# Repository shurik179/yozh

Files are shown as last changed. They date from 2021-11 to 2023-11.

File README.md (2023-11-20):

# Yozh Robot
Yozh is a small tracked  robot programmable in CircuitPython. 
It was  inspired by  Pololu's Zumo, but has numerous improvements over it. 
It was created by shurik179 for a robotics class at SigmaCamp.

The project description and logs are posted on Hackaday: 
https://hackaday.io/project/193665-yozh-robot. 
Detailed  user documentation is available at http://yozh.rtfd.io. 

## Status
Version 4 is mostly finished, working on documentation and fine-tuning 
various PID controllers. 

## Structure of this repository
* `docs`: documentation (used to produce docs at http://yozh.rtfd.io)
* `hardware`: design files for the custom electronics boards, BOM, etc.
* `board_support_package`: bootloader and packeg to have the secondary MCU 
   supported in Arduino IDE. Only needed fro uploading the firmware - end 
   users do not need this. 
* `firmware`: firmware for secondary MCU
* `circuitpython_library`: Circuit Python user library

## License
Ecept as noted below, all components (hardware, software, documentation) are
copyright by Alexander Kirillov  and are  released under MIT license.
See file LICENSE in this directory for full text of the license.

Circuit Python librabries included in circuitpython_library/lib are copyright by Adafruit, see
https://github.com/adafruit/Adafruit_CircuitPython_Bundle . They are released under MIT License.

Fonts included with Circuit Python library are released under SIL Open Font License.
See LICENSE file in directory circuitpython_library/fonts

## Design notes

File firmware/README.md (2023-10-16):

# Yozh  Firmware

This folder  contains the firmware and
necessary support files for Yozh robot.

Since Yozh comes with the firmware pre-installed, most users do not need
any of the files in this directory. You only need to use it if you want to
understand the inner workings of the firmware, or to create your own modified
version of the firmware. Note: the authors of the firmware provide no technical
support for modifying the firmware; do it at your own risk.

## Building the firmware from source
This information is for advanced users only. Use at your own risk!!

It is assumed that you have some experience with Arduino, so the instructions
are brief. This is intentional, to discourage inexperienced users.

To build the firmware from the source, you need the following software installed
on your computer:

1.  Arduino IDE (version 1.8 or later).

2. Board definition files -- see instructions below

3. Required libraries:

   *  FlashStorage

   All of these libraries can be installed using library manager built into Arduino IDE

4. After completing the steps above,  restart the Arduino IDE and select
`Adafruti Crickit M0` in *Tools->Board* menu.

You are now ready to build and upload new firmware from source. Download the
contents of this  repository as a zip file, unpack, and find inside it folder
`firmware/yozh-firmware`. Move it  to Arduino sketchbook folder. Now find in that
folder file  `yozh-firmware.ino` and open it in Arduino IDE. Edit is as you
like and upload to the board in the usual way.

### Board definition files
For step 2 above, you need to install the board definition files for Yozh main
board.  The easiest way to do it is to reuse the board definitions
provided by Adafruit for their Crickit board, just changing some files, as
follows:

1. Install Adafruit's board support package for SAMD-based boards, as described
[here](https://learn.adafruit.com/adafruit-feather-m0-basic-proto/setup). Please
use version 1.5.13, **even if later versions are available** (most likely, using
later versions would also be OK, but it was not tested.)

2. Find the installed package files.  To do this, first find the folder with
Arduino configuration data;  depending on your OS and version of Arduino IDE, it
can be either `<username>\AppData\Local\Arduino15` (Windows),
`<username>\Documents\ArduinoData\` (Windows 10, using Arduino IDE installed
from Windows store), or `/home/<user>/.arduino15/` (Linux).

    Once you found the Arduino configuration data folder, navigate to `\packages\adafruit\hardware\samd\1.5.13\variants\crickit_m0`.

3. Download two files `variant.cpp` and `variant.h` from `boardDefinitions`
folder in this repository and use them to replace the corresponding files in
`crickit_m0` folder.

4. Restart Arduino IDE.

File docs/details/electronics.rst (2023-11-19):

Electronics
===========
The robot is controlled by two microcontrollers (MCU):

* Main (master) MCU: `ESP32-S3 Reverse TFT Feather  <https://www.adafruit.com/product/5691>`__.
  This MCU is programmed by the user in CircuitPython. Provided CircuitPython
  library, documented in :ref:`Yozh Library Guide <library>`, provides convenient
  functions for using all features of the robot.

* Secondary (slave) MCU: SAMD21G18A. This MCU is responsible for all low-level
  operations, converting high-level commands coming from main MCU into signals
  sent to motors, servos and more, thus freeing pins and other
  resources of the main MCU for other purposes.  Secondary MCU  is also responsible for counting
  the encoder pulses and running the PID control loop maintaining motor speed.
  This MCU comes preloaded with firmware, written in C++ (using Arduino IDE).
  Normally, the user shouldn't need to touch this firmware.

The two MCUs talk to each other  using I2C communication protocol; main MCU acts as
the master on the I2C bus, and the secondary acts as slave.

Some of Yozh hardware is directly controlled by the main MCU, without going
through the secondary one:

* TFT  display

* Buttons

* Buzzer

* Distance sensors

* Two indicator NeoPixel leds

* battery voltage monitor

Everything else -- motors, encoders, servos, reflectance sensor
array,  Inertial Motion Unit -- is handled by the
secondary MCU.

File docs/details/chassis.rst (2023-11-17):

Chassis and motors
===================
Yozh robot uses custom-made chassis, using 
`silicone tracks <https://www.pololu.com/product/3034>`__ by Pololu together with two
`75:1 High Power 6V microgear motors <https://www.pololu.com/product/2215>`__. The
motors are equipped with encoders (rotation counters), for speed control. The
motors are controlled by DRV8833 motor driver by TI.

Maximal speed of the robot is FIXME m/s.

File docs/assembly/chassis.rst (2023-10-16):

Assembling the chassis
======================
Take the Zumo chassis kit and open it. Make sure you have all components
as listed in `Zumo chassis user guide <https://www.pololu.com/docs/0J54/1>`__.
Discard the acrylic plate - we wont' be using it.

Now follow these steps:

1. Turn the chassis upside down. Remove the cover  from the battery
   compartment of the chassis and insert the double battery contacts in the
   slots as shown in the photo below, paying attention to orientation.
   Leave two single contacts for later.

2. Insert 4 M2.5 screws from Yozh kit in the
   holes as shown in the photo below. It should be a tight fit -- use a screwdriver
   to drive the screws all the way in.

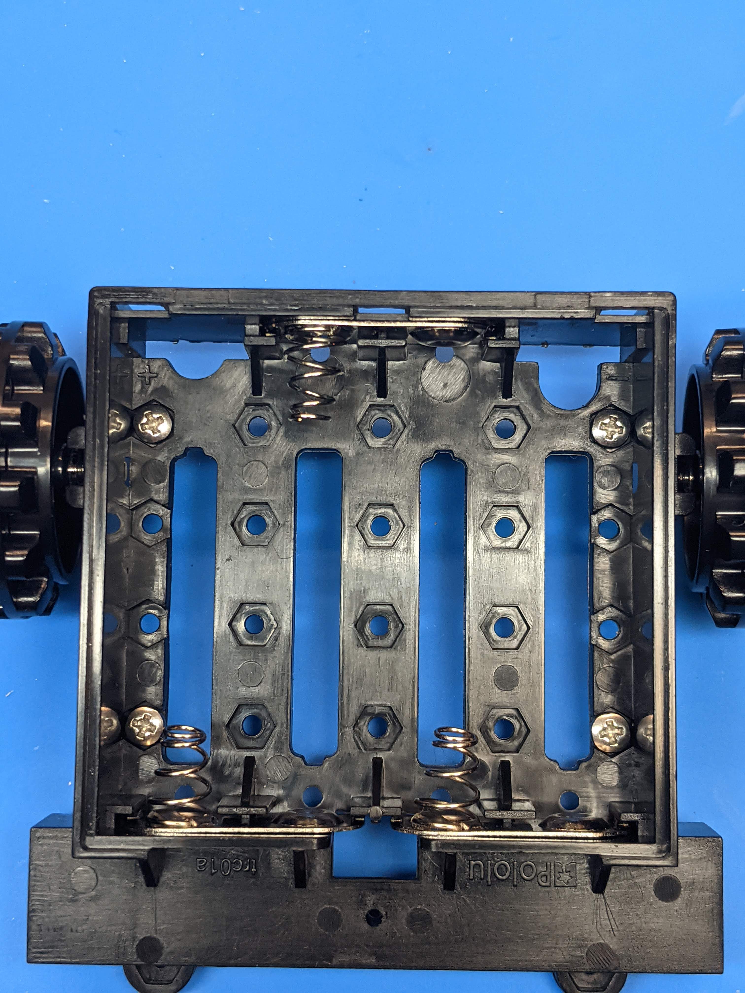
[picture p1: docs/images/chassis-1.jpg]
Chassis assembly 1


3. Turn the chassis right side up. Attach the idler sprockets following the
   directions of `Zumo user guide <https://www.pololu.com/docs/0J54/3>`__.

4. Insert the motors with leads in the channel at the front of the chassis, aligning the
   gearbox with the grooves in the channel. The front plate of the gearbox
   should be even with the edge of the chassis. The motor leads you had soldered previously
   should be facing up.

   (Tip: place a pencil under the center of the chassis)

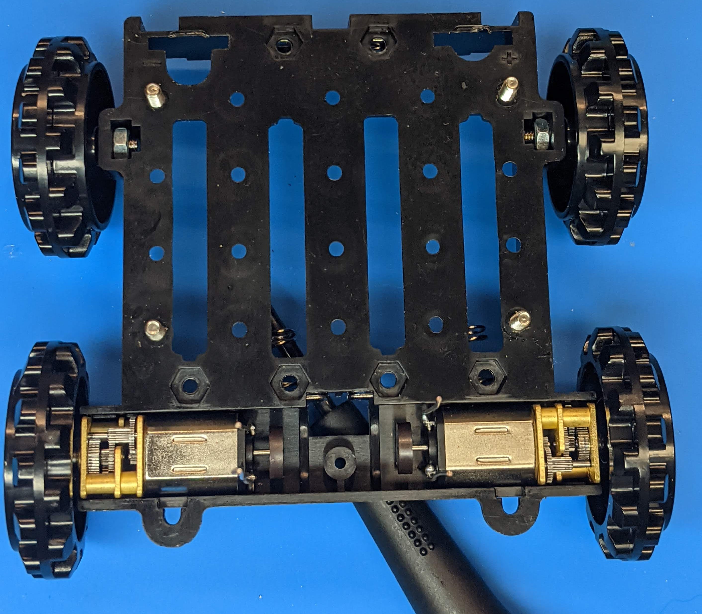
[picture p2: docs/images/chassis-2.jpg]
Chassis assembly 2


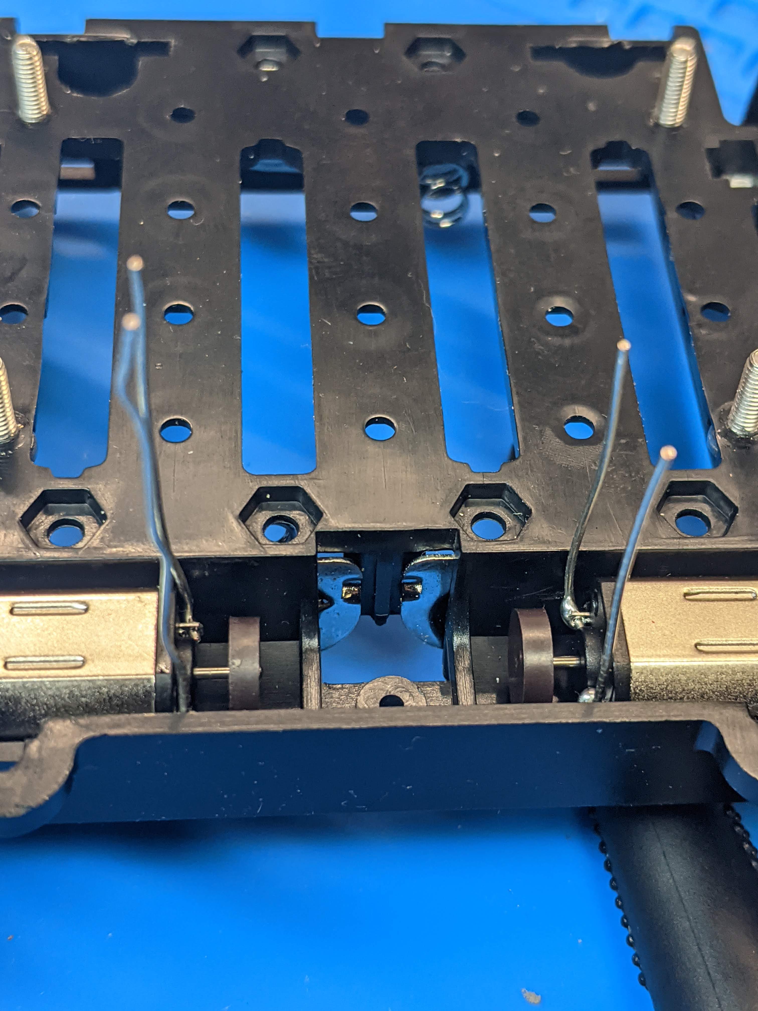
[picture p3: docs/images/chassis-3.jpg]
Chassis assembly 3


5. Take the spacer PCB and place it on the chassis, carefully threading the
   motor leads through the holes in PCB. The screws you had inserted should match
   the holes in the spacer PCB.
   **Warning**: spacer PCB is not symmetric - pay attention to **This side up**
   marking.

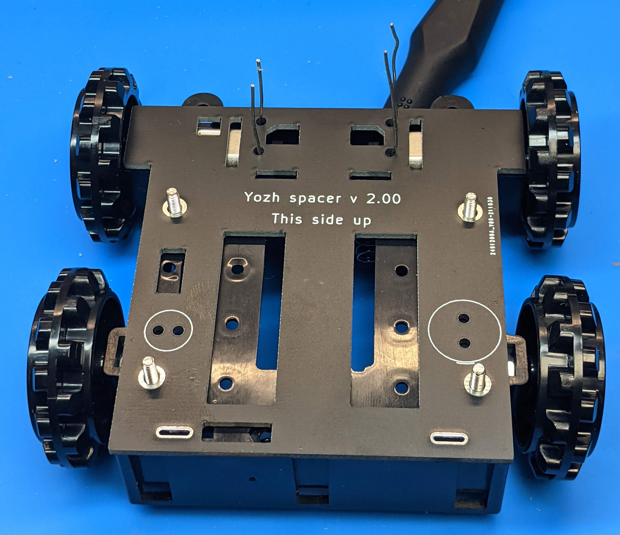
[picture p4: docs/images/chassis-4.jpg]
Chassis assembly 4


6. Repeat the same with the main board. Make sure that this board lies flat
   against the spacer board, with no gaps anywhere.

7. Tightly screw the 22mm M2.5 standoffs from the Yozh kit onto the screws
   protruding through the main board.

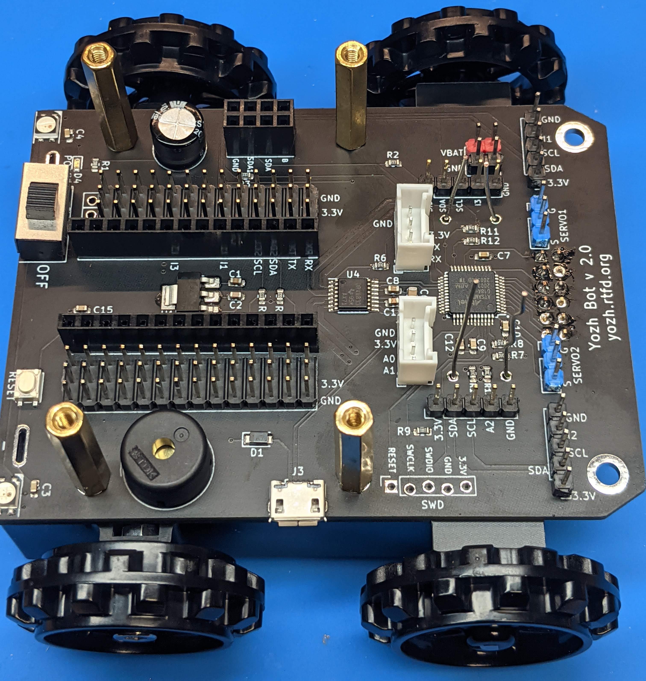
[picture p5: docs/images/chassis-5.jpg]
Chassis assembly 5


8. Put the silicone tracks on wheels (requires a little effort).

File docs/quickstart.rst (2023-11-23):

.. _quickstart:
*****************
Quick start guide
*****************

If you got the Yozh robot as a kit or are building your own from scratch, please
follow the  instructions in :ref:`Yozh Assembly Guide <assembly>` to put your robot together.

Once the robot is assembled, follow the steps below to get started quickly.

.. toctree::
    :caption: Table of Contents
    :maxdepth: 1

    quickstart/at_glance
    quickstart/batteries
    quickstart/installation
    quickstart/thonny
    quickstart/hello_world
    quickstart/serial
    quickstart/functions
    quickstart/examples
    quickstart/further

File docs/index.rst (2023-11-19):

##########
Yozh Robot
##########
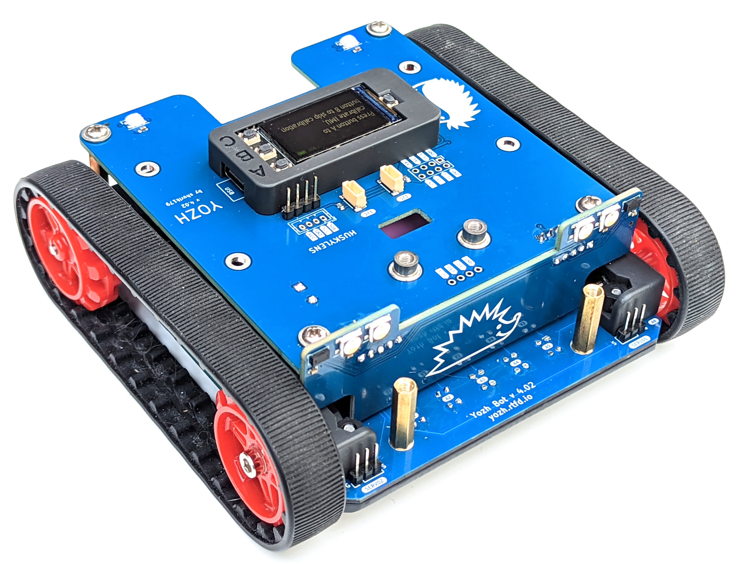
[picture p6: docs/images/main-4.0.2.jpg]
Yozh robot


Yozh is a small (about 13cm*13cm) robot, inspired by  Pololu's Zumo robot. It was
created by `shurik179 <https://github.com/shurik179>`__ for a robotics class at
`SigmaCamp <http://sigmacamp.org>`__. Below are the
key features of this robot.

* **Dimensions:** Length: 12.4 cm; width: 13 cm; height: 4.9 cm

* **Power:** one or two 18650 Li-Ion batteries

* **Wheels and motors:** uses `silicone tracks <https://www.pololu.com/product/3034>`__  and
  `6V, HP, 75 gear ratio <https://www.pololu.com/product/2215>`__ micro metal
  gearmotors, both by Pololu.

* **Main controller:** `ESP32-S3 Feather board  <https://www.adafruit.com/product/5691>`__ by Adafruit,
  which serves as robot brain. It  is programmed by  the user in CircuitPython, using a provided
  CircuitPython library. This library provides high-level
  commands such as *move forward by 30cm*

* **Electronics:** a custom electronics board, containing a secondary MCU (SAMD21) preprogrammed
  with firmware,  which takes care of all low-level operations such as counting encoder pulses,
  controlling the motors using closed-loop PID algorithm to maintain constant
  speed, and more.

* Included sensors and other electronics

    * 240*135 **color TFT  display** and 3 **buttons** for user interaction

    * Bottom-facing **reflectance array** with 7 sensors, for line-following and other similar tasks

    * Two front-facing **distance sensors**, using VL53L0X laser time-of-flight sensors,
      for obstacle avoidance

    * A 6 DOF **Inertial Motion Unit** (IMU), which can be used for determining robot
      orientation in space for precise navigation

    * Two RGB **LEDs** for light indication and a **buzzer** for sound signals

    * Four RGBW LEDs used as headlights 

* Expansion ports and connections:

    * Two ports for connecting **servos**

    * Two  I2C ports, using Qwiic/Stemma QT connector

    * Several available pin headers for connecting other electronics

    * Yozh is compatible with mechanical attachments
      (`grabber <https://www.dfrobot.com/product-2128.html>`__, `forklift <https://www.dfrobot.com/product-2129.html>`__,...) by DFRobot.

All robot design is open source, available in |github| under MIT  License, free
for use by anyone. We also plan to create a Yozh kit which would be sold on
Tindie for those who want to build the robot but do not have time or skill
to assemble their own PCBs.

You can view photos and videos of Yozh here:

https://photos.app.goo.gl/grQfWu86DGW8zRTT8

.. toctree::
    :caption: Table of Contents
    :maxdepth: 1

    quickstart
    details
    library
    projects

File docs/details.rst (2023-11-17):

.. _features:
***************************
Yozh Features in Detail
***************************

Yozh robot
    
.. toctree::
    :caption: Table of Contents
    :maxdepth: 1

    details/dimensions
    details/power
    details/chassis
    details/electronics
    details/top_plate
    details/leds
    details/imu
    details/sensors
    details/connectors
    details/servos

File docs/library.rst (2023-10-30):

.. _library:
**************************
Yozh Library Reference
**************************

In this chapter, we give full list of all commands provided by Yozh Circuit Python
library. We assume that the user has already installed Yozh library on the
robot, as described in the :ref:`Quickstart Guide <quickstart>`.

This document describes version 4.0 of the library. It is intended to be used
with CircuitPython 7.

.. toctree::
    :caption: Table of Contents
    :maxdepth: 1

    library/init
    library/UI
    library/motors
    library/servos
    library/reflectance
    library/distance
    library/imu

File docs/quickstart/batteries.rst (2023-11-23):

Installing the batteries
========================

Yozh is powered by one or two 18650 Li-Ion batteries, inserted in the
battery compartment inside the robot; to access it, you need to remove
the top plate.  

**Warning**: Li-Ion batteries can be dangerous if not handled right! please
make sure to place them with  correct polarity. 
Always **turn the power switch off** before
removing the top plate, replacing the battery,  
or doing any other work on the robot.

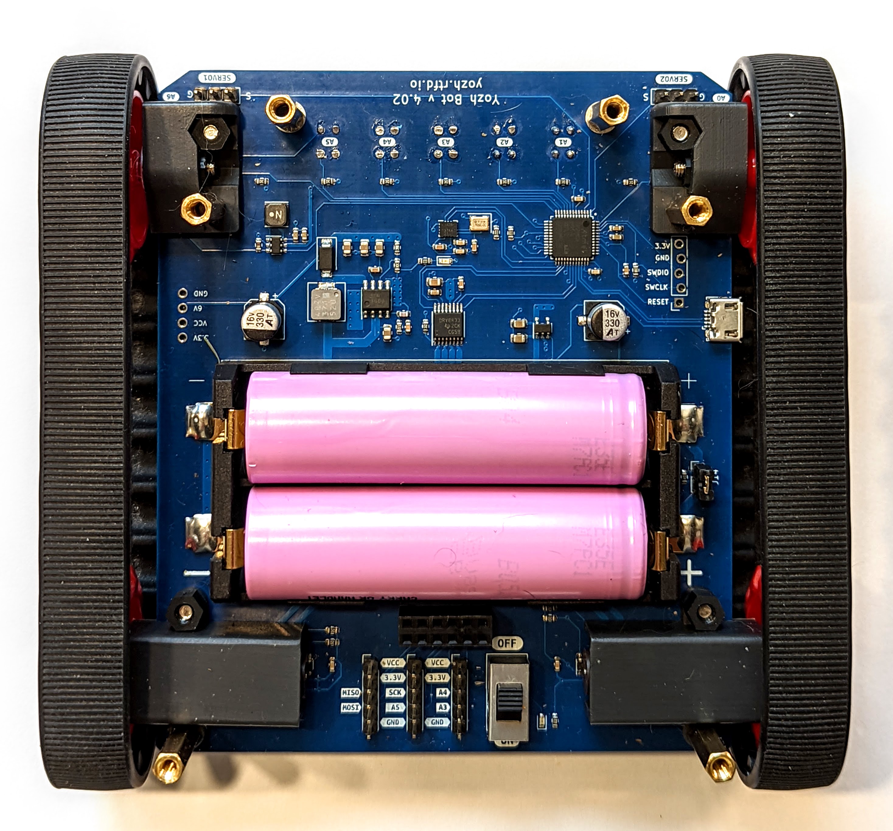
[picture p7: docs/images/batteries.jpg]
Batteries


For most purposes, it suffices to use one battery; 
place it in the slot closest to the back of the robot 
(of course, power switch should be off while you are doing it). Make sure 
to observe correct polarity as labeled on the PCB!

See section ``Power`` in :ref:`Yozh Features in Detail <features>` document 
for suggestions on choosing the best 18650 battery or proper method of 
installation if you want to use two batteries -- there are some precautions to be observed!

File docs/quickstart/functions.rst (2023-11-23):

Commonly used functions
====================================

Below is the list of most commonly used functions from Yozh CircuitPython library. 
This is not a full list! See :ref:`Library reference <library>`  for full list and details. 

To begin using the library, you need to put the following in the beginning of
your `code.py` file:

.. code-block:: python

   import time
   from  yozh import *
   bot = Yozh()

This creates and initializes an  object with name ``bot``, representing your robot.  From now
on, all commands you give to the robot will be functions and properties of ``bot``
object. We will not include the name bot in our references below; for example,
to use a command :func:`stop_motors()` described below, you would need to write
:func:`bot.stop_motors()`.

Display, buttons
----------------
.. function:: clear_display()

   Clears all text and graphics from display

.. function:: set_text(line_number, message)

   Print given message on a given line of the display. Line number can range 0--5. 
   Note: this command supports more options; check the library reference. 

.. function:: wait_for(button)

   Waits until the user presses the given button. There are three  possible
   pre-defined buttons: ``BUTTON_A``, ``BUTTON_B``, ``BUTTON_C``.

There are also functions for checking if a given button is currently pressed, 
or waiting until the user presses one of 3 buttons. 

LEDs, buzzer, headlights
------------------------
.. function:: set_lights(power)

   Turns the headlights on/off. Power should be between 0-100; setting the power to zero 
   turns the headlights off.

.. function:: set_leds(color_l, color_r)

   Set colors of both LEDs at the same time. Each color can be a triple 
   giving values of red, green, and blue (each 0-255) or a hex number:
   ``set_leds( (255,0,0), 0xFF0000)``. You can also use one of predefined colors: 
   RED, GREEN, BLUE, YELLOW, WHITE, OFF, e.g. ``set_leds(BLUE)``. 
   Parameter ``color_r`` is optional; if omitted, both LEDs will
   be set to the same color.

.. function:: buzz(freq, dur=0.5)

    Buzz at given frequency (in hertz) for given duration (in seconds).
    Second parameter is optional; if omitted, duration of 0.5 seconds is used.

Driving
-------
.. function:: go_forward (distance, speed=60)

.. function:: go_backward(distance, speed=60)

   Move forward/backward  by given distance (in centimeters). Parameter ``speed``, which ranges 
   between 0-100,  is optional; if not given, default speed of 60 is used.
   Note that distance and speed should always be positive, even when moving backward.

   Behind the scenes, these commands try to maintain constant robot speed and direction. 
   To learn more about how it is done check section FIXME.  

.. function:: turn(angle, speed=60)

   Turn by given angle, in degrees. Positive values correspond to turning right (clockwise).
   Parameter ``speed`` is  optional; if not given, default speed of 50 (i.e. half of maximal) is used.

.. function:: set_motors(power_L, power_R)

   Set power for left and right motors. ``power_L`` is power to left motor,
   ``power_R`` is power to right motor. Each of them should be  between 100
   (full speed forward) and -100 (full speed backward).

   Note that because no two motors are exactly identical, even if you give
   both motors same power (e.g. ``set_motors(60,60)``), their speeds might be
   slightly different, causing the robot to veer to one side instead of moving
   straight. To avoid this, use ``go_forward()`` command described above. 

.. function:: stop_motors()

   Stop  both motors.

Inertial Motion Unit (IMU)
--------------------------
Before use, the IMU needs to be calibrated. The calibration process determines
and then applies corrections (offsets)  to the raw data; without these
corrections, the  data returned by the sensor is very inaccurate.

If you haven't  calibrated the sensor before (or want to recalibrate it),
use the following function:

.. function::  IMU_calibrate()

       This function will determine and
       apply the corrections; it will also save these corrections in the
       flash storage of the Yozh secondary microcontroller, where they will be
       stored for future use.  This data is preserved even after you power
       off the robot (much like the usual USB flash drive).

       This function will take about 10  seconds to execute; during this time,
       the robot must be completely stationary on a flat horizontal surface.

If you had previously calibrated the sensor, you do not need to repeat the
calibration process - by default, upon initialization the IMU loads previously
saved calibration values.

.. function:: IMU_yaw()

   Returns robot yaw, i.e. heading in horizontal plane. Note that zero heading 
   is rather random (it is not the starting position of the robot!). Positive 
   values correspond to turning right (clockwise). 

Reflectance array
-----------------
.. function:: linearray_on()

.. function:: linearray_off()

   Turns reflectance array on/off. By default, it is off (to save power).

.. function:: calibrate()

   Calibrates the sensors, recording the black  values. This
   command should be called when all  of the sensors are on the black  area of the field.
   This is necessary for the commands below. 

.. function:: sensor_on_white(i)

.. function:: sensor_on_black(i)

   Returns ``True`` if sensor ``i`` is on white (respectively, black) and false otherwise. Index `i` 
   ranges from 0 (rightmost sensor) to 6 (leftmost)

.. function:: all_on_white()

.. function:: all_on_black()

   Returns ``True`` if all sensors are  on white (respectively, black) and false otherwise.

.. function:: line_position_white()

.. function:: line_position_black()

   Returns a number showing position of the line under the robot, assuming white 
   line on black background (respectively, black line on white background). 
   The number ranges between -4 (line far to the left of the robot) to 
   4 (line far to the right of the robot). 0 is central position: line is exactly 
   under the center of the robot. See :ref:`Library reference <library>` for details.

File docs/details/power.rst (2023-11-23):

Power
=====

Batteries
---------
Yozh is powered by one or two 18650 Li-Ion batteries, inserted in the
battery compartment inside the robot; to access it, you need to remove
the top plate.  See the section below for discussion of whether you
need one or two batteries.

**Warning**: Li-Ion batteries can be dangerous if not handled right! please
make sure to place them with  correct polarity, and follow the instructions in the
next section if you use two batteries. Always turn the power switch off before
removing the top plate or doing any other work on the robot.

It is highly recommended that you use batteries from a trusted manufacturer,
such as Panasonic, Samsung,  or Sanyo; do not try to save a couple of dollars by
buying a no-name battery from   Amazon or  eBay - instead, use one of
specialized shops such as https://www.18650batterystore.com/.  You need  **flat
top unprotected batteries**; look for batteries with capacity 3000 mAh or more.
Current rating is less important (you need a battery rated for 4A continuous
current or more  -- this is  low by the standards of 18650 battery cells). A
good choice is this battery:
https://www.18650batterystore.com/products/samsung-35e

The robot also contains power switch, for disconnecting the battery, and a
power indicator LED.
You can check the battery voltage in software, using ``battery_voltage()`` function as
described in  :ref:`Yozh Library Guide <library>`. Fully charged Li-Ion batteries
should read about 4.2v.

One or two batteries?
---------------------

For most purposes, one 18650 battery is sufficient. Place it in the slot
closest to the back of the robot. **Make sure to place it with correct polarity;**
positive and negative terminals are labeled on the robot PCB.

If you are planning on using accessories that might use significant current,
such as large size servos or AI cameras, or if you want to run the robot for
long periods, you might want to add a second battery; these two batteries will
be connected in parallel.

If you want to use two batteries, please observe these precautions. Please
take them seriously!

* it is best to use the two identical batteries (same manufacturer and model)

* before inserting the batteries, turn the power switch to off and **remove the
  jumper  J14** next to the batteries. After this, insert the batteries; 
  **make sure to place them with correct polarity** as labeled on the PCB. 
  Leave
  them inserted for a couple of hours or so, keeping the power switch off. After
  two hours, put the jumper J14 back on.    (This allows the
  two batteries to equalize the voltage. The positive terminals are connected
  through on-board 1 Ohm resistor. Jumper J14 shorts it.)

Batteries

Voltages used by the robot
--------------------------
The robot contains a voltage regulator, which converts battery voltage
to regulated 3.3v. This regulator provides power to the secondary MCU, IMU
and distance sensors, leaving about 300 mA available for use by extra sensors
you might connect to  Yozh.

Yozh also contains a boost converter, converting battery voltage to regulated 6V.
This is used to power the motors and servos.

Finally, some of the on-board electronics are powered directly from the battery voltage:
the main MCU and TFT  screen, Neopixels and headlights.

Connecting the ESP32-S3 microcontroller to a computer by USB cable provides power
to the MCU  even if the main battery is off. This would activate the main  MCU
and some of the electronics, but not the secondary MCU, motors or servos.

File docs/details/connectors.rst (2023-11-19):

Connecting additional devices 
=============================
Youzh provides connectors for additional sensors and other eelctroncis, as described below. 

Top plate
---------

The top plate contains the following connectors:

* two Qwiic/StemmaQT connectors, for connecting I2C sensors. These connectors use the 
  default I2C pins of ESP32-S3 board. The same I2C bus is also used for connecting to 
  secondary MCU (I2C address 0x11) and distance sensors (I2C addresses 0x29, 0x30); 
  thus, make sure that the devices you connect have I2C addresses different from those 
  listed above. Pull-up resistors (3.3K) on SCL and SDA lines are already provided, 
  so there is no need to add your own. 

* 8-pin connector (unpopulated), containing pins for 3.3v, GND, and pins A1, A2, TX, RX
  of ESP32-S3 

* Huskylens connector. This is also gives access to the same  I2C bus; however, instead of 3.3V, 
  it provides VCC, which is directly connected to the battery (thus, voltage ranges from 4.2-3.5V 
  depending on battery charge.) In addition, the pin order is different from the one used by Qwiic. 
  This connector provides both standard male pin headers and JST PH 4-pin connector, which share 
  the same pins. This connector is primarily intended for connecting Huskylens AI camewra by DFrobot, 
  but coudl also be utilized by other devices as long as they are capable of using the battery voltage. 

  Note that the SDA and SCL lines are pulled up to 3.3v, not to VCC. 

Top view of the robot

Main board connectors
---------------------

In the rear of the main robot board, there are even more connectors, providing access to SPI 
(MISO/MOSI/SCK) pns of ESP32-S3 and pins A3, A4, A5 (you can use one of them as chip select 
line for SPI). 

Note that  the SPI bus is also used for communication with the display. 

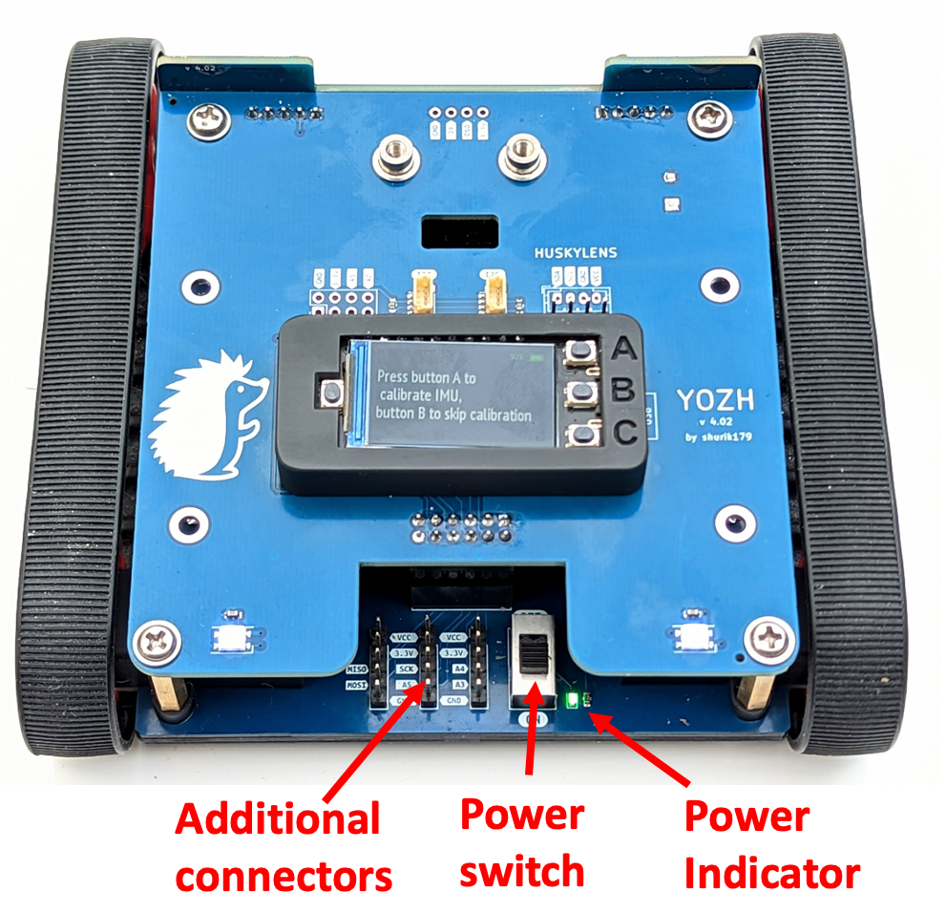
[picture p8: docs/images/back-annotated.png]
Rear view


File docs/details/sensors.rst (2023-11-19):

Distance and reflectance sensors
=======

Yozh robot has several built-in sensors.

Reflectance array
-----------------
In the front of the robot, there is an array of 7 down-facing reflectance
sensors for detecting field borders, following the line, and other similar tasks.
It uses `ITR9909 <https://lcsc.com/product-detail/Reflective-Optical-Interrupters_Everlight-Elec-ITR9909_C53399.html>`__ sensors
by Everlight. The sensors are labeled A0 (rightmost) through A6 (leftmost).

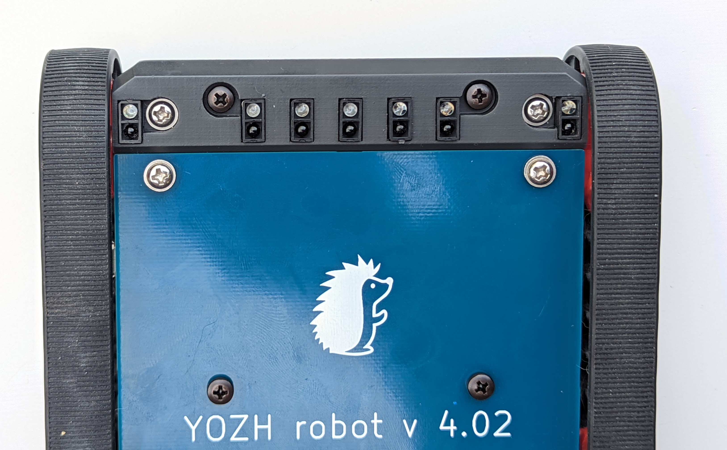
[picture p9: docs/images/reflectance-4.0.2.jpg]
Reflectance array


Distance sensors
----------------

Yozh also contains a front-facing board with two  `VL53L0X
<https://www.st.com/en/imaging-and-photonics-solutions/vl53l0x.html>`__
Time-of-Flight laser distance sensors by ST Microelectronics. These sensors
have maximal distance of 2m; reliable sensing distance is closer to 1.5m.
Each sensor has 25 degree field of view; this leaves a very small "blind spot" immediately
in front of the robot, but provides complete coverage enabling the robot to
detect any  obstacle placed between 15-150 cm away.

These sensors  can be used for obstacle avoidance, object tracking,
or other similar purposes.

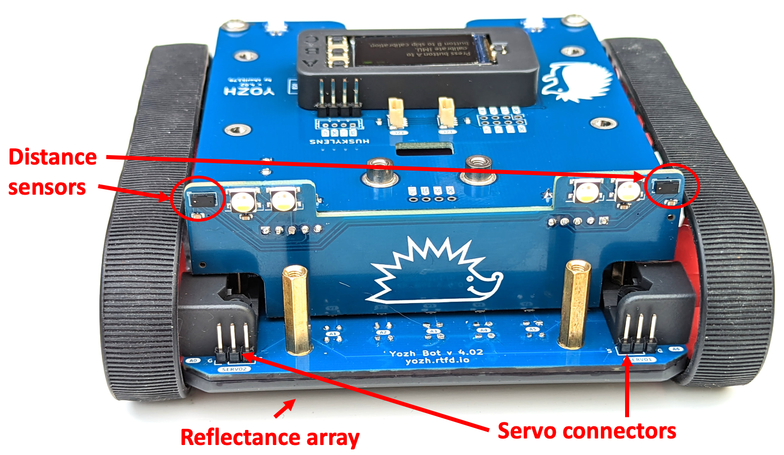
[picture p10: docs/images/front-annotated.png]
Front view


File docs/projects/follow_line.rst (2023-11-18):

Line follower
=============

In this chapter, we program the robot to follow a line on the floor.
We will make a line by putting 1/2-inch wide
white gaffers tape on a black surface (a sheet of plywood painted black).
You can make your own field; just make sure the line is at least half  inch
wide and doesn't have sharp turns.

Before we start writing code, we need to describe the algorithm the robot
will be using - first in human language, then translate it to Python.

The obvious algorithm is "start on the line; go forward until you get off
the line; turn to get back on the
line; repeat".

However, this algorithm will result in very jerky movement: the robot
will only start correcting its course when it gets completely off the line.
Since we have a whole array of front line sensors, we can use them
to detect even small deviation from the right course - when the robot is still
on the line, but the line is not exactly under the center of the robot - and start
correcting before we get off the line. Yozh library provides a function that allows one
to determine the position of the line relative to the center of the robot:
`line_position_white()`, which returns values ranging from -5 to 5.

To correct, we would be going forward but
steering more to the left or right as needed: if the line is to the left of the robot
center, we must be steering left; if the line is to the right, we must be steering right.

This leads to the following algorithm

.. code-block:: python

    while True:
        get the line position
        go forward steering left or right as needed to correct the position

Note that here we are continuously correcting our steering using the sensor
feedback.  To translate this algorithm to an actual program, we need to
explain how one steers left or right.  This is easy: to have the robot
steer to the right, we need left motor to have more power than the right.
Thus, instead of having both motors running at 50%, we could use
 `setMotors(50+correction, 50-correction)`.
It makes sense to have the parameter `correction`  **proportional** to the
difference between the actual line position and the desired one: the
farther off we are,  the more we need to turn.

This gives the following program

.. code-block:: python

    Kp = 9
    while True:
        error = bot.line_position_white()
        bot.set_motors(50+Kp*error,50-Kp*error)

Double-check the sign: if `error` is negative (line to the left), we need to
be steering left, so the left motor should have less  power than the right;
if `error` is positive, we will be steering right.

The value of the coefficient `Kp=9` was chosen so that when the line is
all the way to one side (error= -5), the motors will be given power
50+45=95, 50-45=5

You can test what happens if Kp=9 is replaced by another value. If the
value is too large, the robot will turn very quickly even for small
errors, which can lead to the robot spending most time turning left
and right, with very little headway. If the value is too small, the
robot will be turning very little, which can cause it to miss a sharp
turn. You can experiment to find the best value.

The same idea of correcting the course using sensor feedback, with
the correction proportional to the error, can be used in many
other situations. Instead of following the line, we could use it
to turn to  face an obstacle (using front proximity sensors), or
face up on an inclined surface, or many other similar situations.

The code above still has one problem. Namely, when we reach the end of the
line, function `line_posiiton_white()` will return `None`, which will cause
an error in the next line: you can't use `None` in an arithmetic expression.
Thus, we need an extra check to catch that.

A natural idea would be to replace `while True` by `while error is not None`:

.. code-block:: python

    Kp = 9
    while bot.line_position_white() is not None:
        error = bot.line_position_white()
        bot.set_motors(50+Kp*error,50-Kp*error)

This, however, is not enough - do you see why?

Better version is using ``break`` command of Python: 

.. code-block:: python

    Kp = 9
    while True:
        error = bot.line_position_white()
        if error is None:
            break 
        bot.set_motors(50+Kp*error,50-Kp*error)
    bot.stop_motors()

As before, you also need to include the code for initialization and sensor
calibration.

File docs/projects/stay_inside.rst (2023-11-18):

Stay inside the field
=====================

We begin with a very simple project: staying in the field. Here, we assume
that we have a black field (such as black painted plywood) with boundary
marked by white tape. The goal is to program the robot to stay within the field
boundaries.

First attempt (in pseudocode, not including the intialization):

.. code-block:: python

    go forward until robot sees white boundary
    turn around

To see the boundary, we use reflectance sensor array, namely function
`all_on_black()`: if this function returns `False`, at least one of the sensors
sees the white boundary. We also replace "go forward until..." by more common `while` loop:

.. code-block:: python

    bot.set_motors(30,30)
    while bot.all_on_black():
        pass
    #if we are here, it means at least one of sensors sees white
    bot.stop_motors()
    bot.turn(180)

Note that there is no need to set motor speed inside `while bot.all_on_black()`
loop: the motors are already running and will continue doing so until you
explicitly stop them .
`

Finally, we enclose it in `while True` loop to make it repeat forever:

.. code-block:: python

    while True:
        bot.set_motors(30,30)
        while bot.all_on_black():
            pass
        #if we are here, it means at least one of sensors sees white
        bot.stop_motors()
        bot.turn(180)

This is far from optimal. For example, if it is the right sensor that sees the
boundary, it makes sense to turn left rather than turn 180 degrees:

.. code-block:: python

    while True:
        bot.set_motors(30,30)
        while bot.all_on_black:
            pass
        #if we are here, it means at least one of sensors sees white
        if bot.sensor_on_white(bot.A1):
            turn(-120)
        else:
            turn(120)

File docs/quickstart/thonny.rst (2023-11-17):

Thonny editor
=============

We suggest using `Thonny editor <https://thonny.org/>`__ for creating and editing
programs for your robot. Experienced programmers can use their favorite text editor instead - but
please check `this page <https://learn.adafruit.com/welcome-to-circuitpython/recommended-editors>`__
for some common problems and list of recommended editors.

To install Thonny,  visit `Thonny webpage <https://thonny.org/>`__, download the installer for 
your system and run it. 

After installation, you also need to configure Thonny to use the CircuitPython interpreter. 
Go to ``Run`` menu and select ``Configure Interpeter``. Select ``Circuit Python (Generic)``. 
While you are there, you can also adjust the theme and font to your liking -- for example, 
you can switch to dark theme, shown below. After making your choices, click ``OK`` to 
save the configuration. 

To verify the installation, connect your computer to the ESP32-S3 MCU of Yozh robot. 
Hit the red ``Stop`` button to reconnect to the board. Thonny should now show the files 
on the CURCUITPY drive,  as shown below:

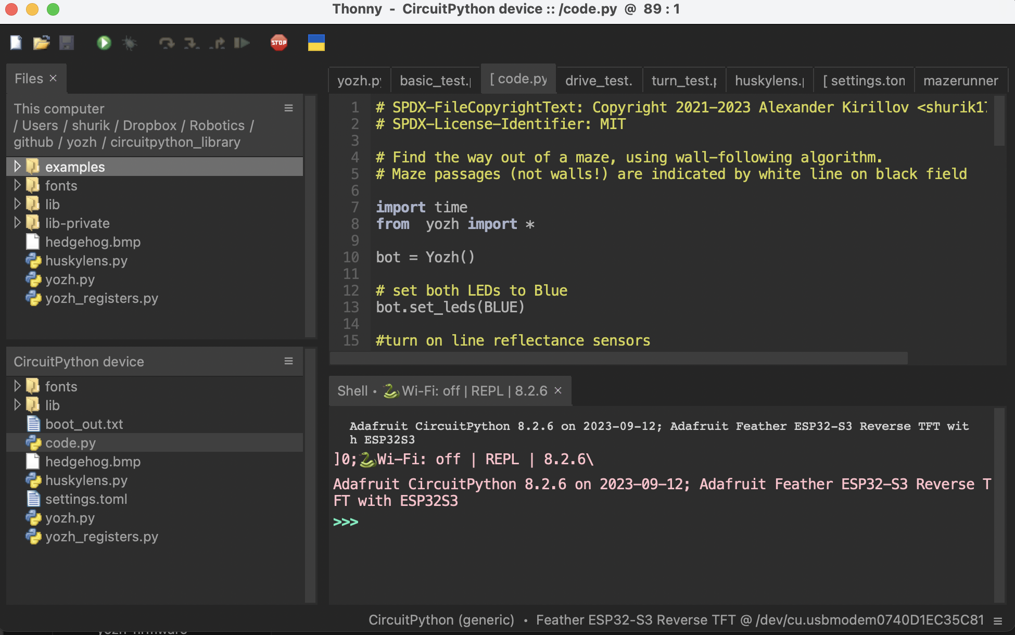
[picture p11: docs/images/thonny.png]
Thonny editor


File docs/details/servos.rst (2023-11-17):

Servos and attachments
======================
Yozh contains two ports for connecting servos, as shown in the photo below.
These ports use  standard pin order: GND, 6V, SIGNAL. To help you identify the
pins, there are small letters S (Signal) and G (GND) next to corresponding pins.
6V pin  is connected to the boost converter that converts battery voltage to 6V. 

Yozh can also be used  with mechanical attachments (`grabber <https://www.dfrobot.com/product-2128.html>`__,
`forklift <https://www.dfrobot.com/product-2129.html>`__,...) by DFRobot --
see photo below for Yozh with the forklift attachment. US customers
might find it easier to order DFrobot kits from DigiKey:

  * `Grabber <https://www.digikey.com/en/products/detail/dfrobot/ROB0156-B/13545231>`__

  * `Forklift <https://www.digikey.com/en/products/detail/dfrobot/ROB0156-F/13545230>`__

  * `Loader <https://www.digikey.com/en/products/detail/dfrobot/ROB0156-L/12324924>`__

Note that some of these attachments might interfere with the distance sensors.

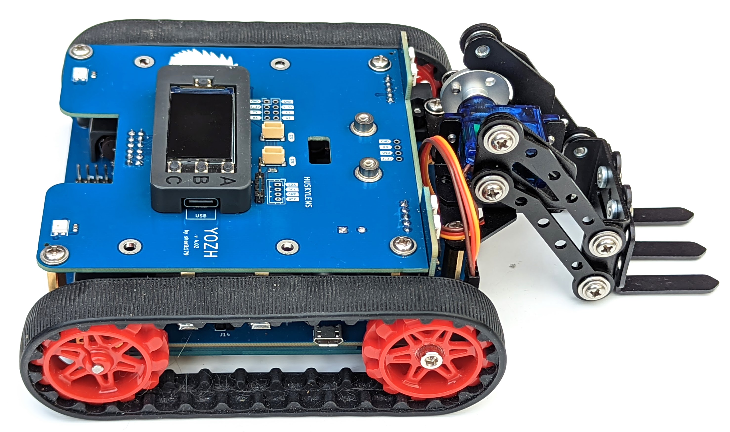
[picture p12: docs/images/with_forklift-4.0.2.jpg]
Yozh robot with the forklift attachment


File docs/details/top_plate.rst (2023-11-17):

Top plate
=========
On the top of Yozh robot, there is a top plate containing the following
elements:

* The main MCU (`ESP32-S3 Feather  <https://www.adafruit.com/product/5691>`__ ), with 
  240x135 color TFT display, reset button, and  
  three  buttons (labeled A, B, C) for user interaction 

* two Qwiic/Stemma QT I2C connectors 

* several  connectors for connecting additional electronics (see FIXME for details)

* a number of 3mm mounting holes for attaching additional electronics

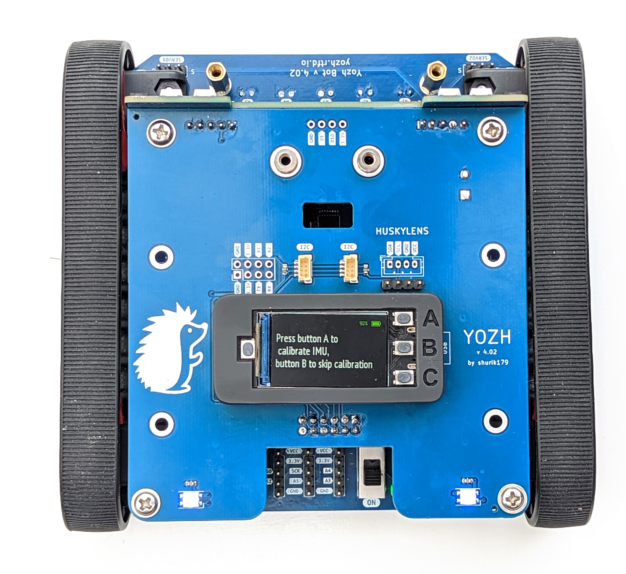
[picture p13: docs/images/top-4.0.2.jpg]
Top view of the robot


The top plate is mounted on the robot using 20mm long M3 standoffs. If
necessary, it can be removed to access the robot interior. **Warning**: 
always turn the robot off before removing the top plate or doing any other 
work on the robot. 

The diagram below shows dimensions and hole locations.

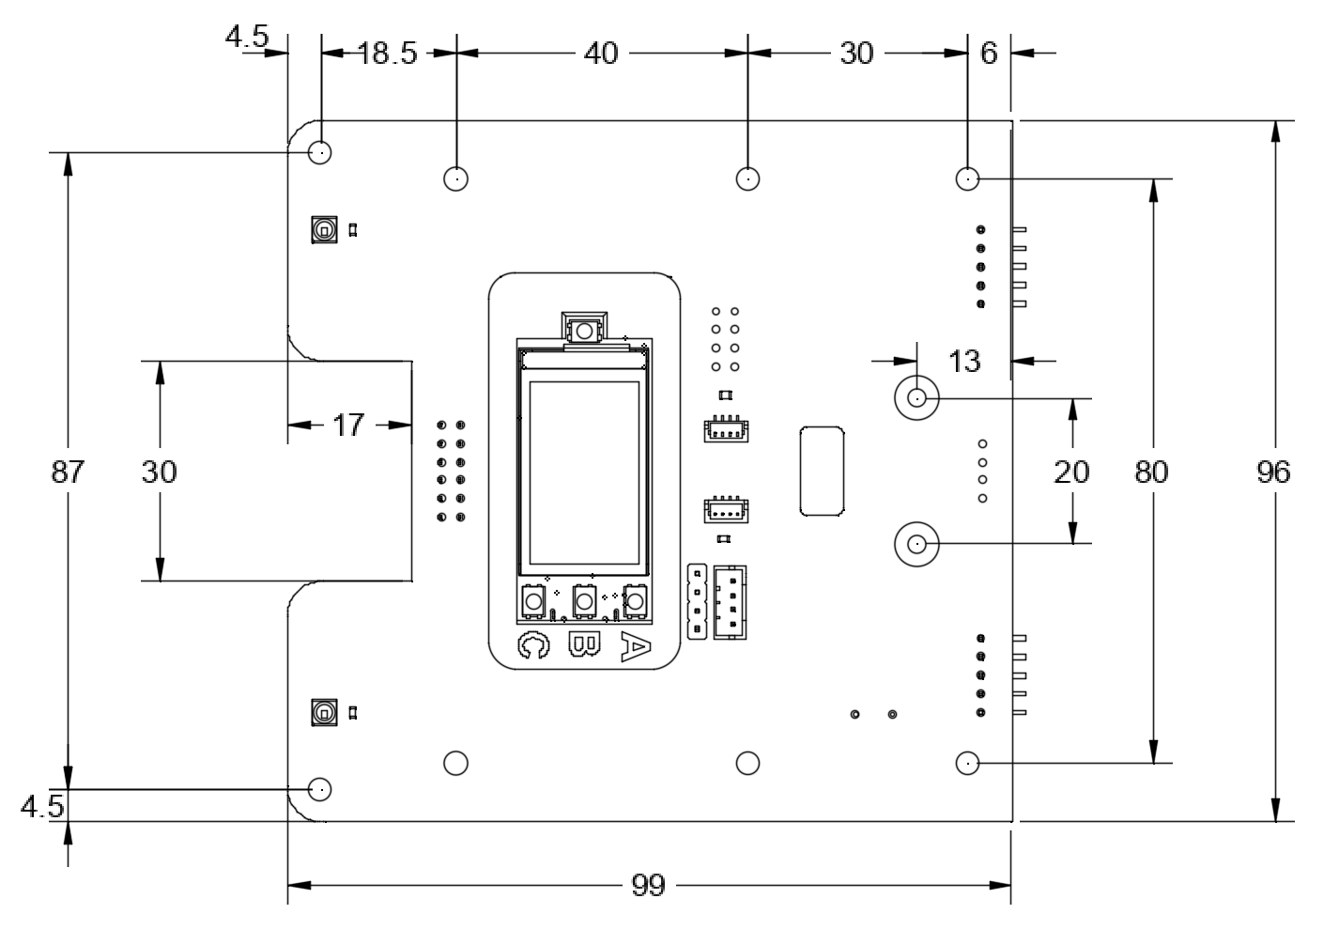
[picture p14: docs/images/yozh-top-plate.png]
Top plate engineering drawing


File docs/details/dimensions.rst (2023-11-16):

Dimensions  and 3d model
========================

Yozh dimensions are 12.4 cm (Length) * 13 cm (width) * 4.9 cm (height).
Ground clearance is about 7 mm; however, since all sensors and everything else
is inside the tracks profile (looking from the side), the robot is capable of
going over (long) obstacles up to about 1.5 cm.

You can view the 3d model, created in Fusion360, at https://a360.co/40igAyW

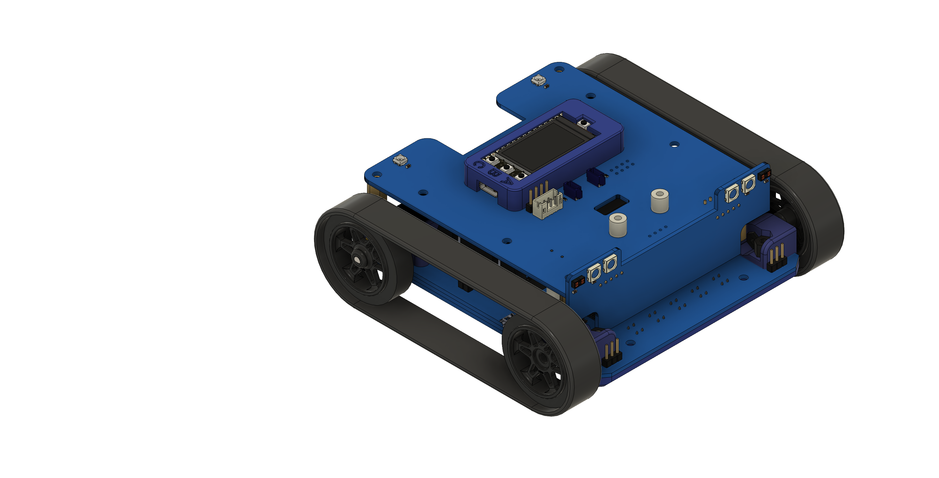
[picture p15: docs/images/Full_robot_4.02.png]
Full robot 3d model


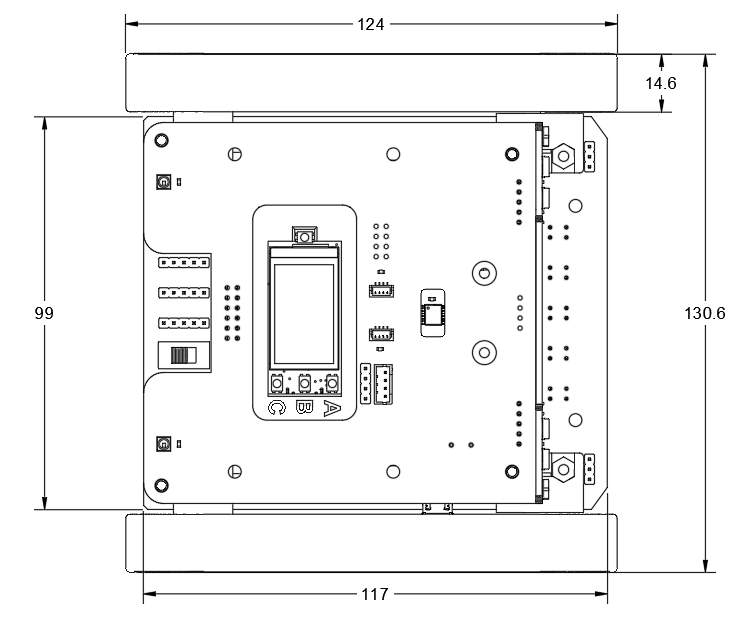
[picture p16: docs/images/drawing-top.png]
Robot drawing - top view


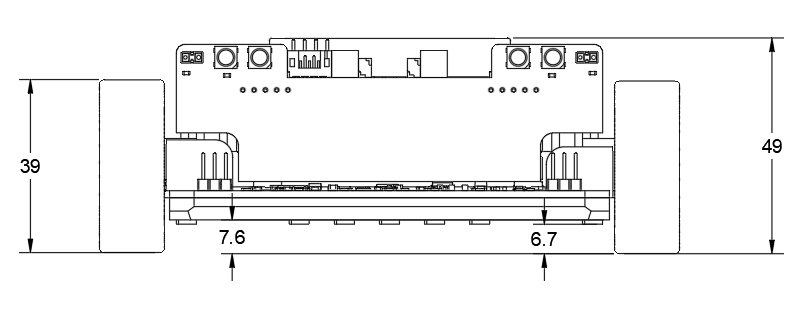
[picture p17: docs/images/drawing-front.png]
Robot drawing - front view


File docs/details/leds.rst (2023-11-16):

Buzzer and LEDs
===============
Yozh contains a buzzer and two addressable RGB LEDs (commonly called NeoPixels),
which can be used for showing information to the user.

Finally, Yozh contains four RGBW NeoPixels of the front panel, which are intended to
be used as headlights. Normally, one only uses the white LED part of these NeoPixels;
however, if necessary, you can also use the RGB part to create headlights  of any color.

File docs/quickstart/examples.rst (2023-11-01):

More examples
=============
Now that you have learned how to write and save programs to the robot,
it is time to explore Yozh capabilities. To help with that, we have provided a
number of examples, which can be found in `examples` folder of the Yozh library
you had downloaded previously. Try opening and running them to see what the robot can do.

 Below is the list of provided examples (as of Nov 1, 2023):

* `basic_test.py` - basic test of robot operation, including OLED display, LEDs, and buttons
* `motor_test.py` - testing basic operation of motors and encoders
* `drive_test.py` - testing higher-level drive commands, such as
  `go forward for 10cm` or `turn 90 degrees`
* `servo_test.py` - testing servos (if you have any attached).
* `imu_test.py`  - testing IMU
* `pid_test.py` - testing PID control of motors
* `distancesensors_test.py` - testing operation of front-facing distance sensors
* `linearray_test.py` - testing reflectance sensor array
* `line_following.py` - following a line (requires a white line 1-3 cm wide, on black background)
* `obstacle_avoidance.py`  - moving around and using distance sensors to avoid obstacles

All of these examples are amply commented, so it should be easy to understand
how the  code  works and how to modify it.

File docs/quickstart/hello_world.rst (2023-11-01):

First program
=============

The `CIRCUITPY` drive which was created during installation of CircuitPython on
EPS32-S3  contains a special file, `code.py`. This file always contains
the code of the  current program running on the board. As soon as you turn the
robot on or hit reset, the robot starts  executing this program.

To test the robot, connect it to the computer, using the USB-C connector of the
ESP32-S3. **Make sure the robot switch is
in ON position**. Start  Thonny   editor and open `code.py` file in `CIRCUITPY` drive,
by clicking on it in the navigation pane on the left or using ``File->Open`` menu item.   
Erase everything in that file so it is blank.

Now, use the top part of the navigataion panel to open the  folder with 
examples from Yozh library you downloaded previously. In that folder, 
find the file `basic_test.py` and click on it to open it in another tab of Thonny 
editor. Copy the whole contents of `basic_test.py`
file and then paste it in `code.py` file. 

Now  click on the green ``Run`` button on Thonny toolbar 
to save `code.py` file and run it. The robot will execute your first program!
Look at the OLED screen, read the prompts, press the buttons, and have fun.

The code is amply commented, so it is easy to make changes.

Note: after running the code, or after disconnecting and reconnecting the robot  to the computer, 
you need to again hit the ``Stop`` button for the editor to reconnnect to the robot. 
Try modifying the code (e.g. changing the text printed to screen) and then
re-save it.

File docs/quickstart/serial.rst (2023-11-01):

Serial console
==============
For debugging the program, one needs  to print some
information such as variable values and error messages. Python has built-in command
`print()` which does that. The output of print command is sent to `serial console` -
which in practice just means that it is sent over USB to the computer.

Thonny  editor has built-in serial console, so you can see these messages. 
By default, the  serial console appears at the bottom of the screen.

Among other features it provides is the ability to enter Python commands
interactively in the console, without saving them to a file - this is very
useful for testing various things. This is called REPL (Read-Evaluate-Print Loop);
see https://learn.adafruit.com/welcome-to-circuitpython/the-repl for more info.

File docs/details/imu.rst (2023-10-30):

Inertial Motion Unit
====================

The robot also contains an inertial motion unit (IMU):
`ICM 42688 <https://invensense.tdk.com/products/motion-tracking/6-axis/icm-42688-p/>`__ by
Invensense. This chip contains an accelerometer and a gyroscope,
allowing the user to measure acceleration and rotation velocity. In addition
to  raw readings, the secondary MCU also runs a sensor fusion algorithm which
uses the accelerometer and gyro data to constantly compute robot orientation
in space, giving yaw, pitch, and roll angles. This can be used for precise
navigation.

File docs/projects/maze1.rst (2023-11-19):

Maze runner: wall following
============================
In this challenge, we will teach the robot find its way out of a maze.
The maze is made of approx. 3x5 ft sheet of plywood, painted black.
White masking tape (3/4 inch  wide) is used to mark passages
forming the maze; these lines follow rectangular grid with
0.5 ft squares.

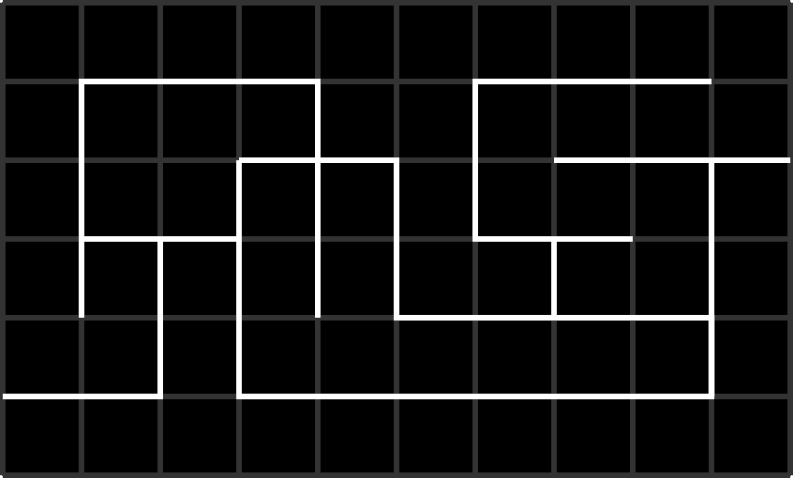
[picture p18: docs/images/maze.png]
Front view


Finding a way out of a maze is a classic problem, and there is a number of algorithms
for doing that. The simplest of them is the wall following rule.

Start following passages, and whenever you reach a junction always follow the
leftmost open passage. This is  equivalent to a human walking in the  a maze by
putting his  hand on the left wall and keeping it on the wall as he walks through.

This method  is guaranteed to find an exit if we start at the entrance
to the maze; then  this method allows us to explore a section
of the maze and find our way out. However, it  is not guaranteed to
find an exit if we start in the middle of the maze: the robot could be
going in circles around an "island" inside the maze.

The first draft of the program looks as follows (not including initialization
and setup):

.. code-block:: python

    while True:
        go_to_intersection()
        check_intersection()
        if there is a passage to the left, turn left
        otherwise, if there is a passage forward, go forward
        otherwise, turn right

Function `go_to_intersection()` should follow the line until we reach an
intersection (that is, until the reflectance sensors at the front of the robot
are above an intersection). This function is very similar to line follower algorithm
from the previous project, with added checks: it should stop when reflectance
sensor A1 (rightmost) or A8 (leftmost) sees white.

Function `check_intersection()` should do three things:

1. Slowly advance forward until  the center (not front!)  of the robot is
   above the intersection.

2. While doing this, keep checking  whether there is a passage to the left
   and record it somehow; same for passage to the right

3. once we advanced  so that the center of the robot is above the intersection,
   also check if there is a passage forward.

We can achieve this by asking the robot to start moving  forward until
we have travelled 5 cm;  while doing this, we will be checking the
line sensors. If the leftmost line sensor (number 6)  sees white, it means that
there is a passage to the left. To record it, we can create boolean variable
`path_left` and set it to `True` once the sensor 6 sees white
(Also, we should remember to set it   to `False` initially):

.. code-block:: python

   def check_intersection():
       # go forward while checking for intersection lines
       bot.reset_encoders()
       path_left = False

       bot.set_motors(30,30) #start moving forward slowly
       while bot.get_distance()<5:
           if bot.sensor_on_white(6):
               path_left = True
       bot.stop_motors()

We should also add similar code for determining whether there is a path to
the right (left to the reader as an exercise).

Next, once we advanced, we need to check if there is a passage ahead.
This is easy using `all_on_black()` function (if there is no passage forward,
all sensors will be on black).

Finally, we need somehow to return this information to whatever place in our
program called this function. If we needed to return one value, we could just
say `return(path_left)`, but here we need to return 3 boolean values:
`path_left`, `path_forward`, `path_right`. One way to do that is to put them in  a list and
return the list. This gives the following code:

.. code-block:: python

   def check_intersection():
       # go forward while checking for intersection lines
       bot.reset_encoders()
       path_left = False
       path_forward = False
       path_right  = False

       bot.set_motors(30,30) #start moving forward slowly
       while bot.get_distance()<5:
           if bot.sensor_on_white(6):
               path_left = True
           ....
       bot.stop_motors()
       if not bot.all_on_black():
           path.forward = True
       # now, let us return the found values
       return([path_left, path_forward, path_right])

Now we can write the main program:

.. code-block:: python

   while True:
       go_to_intersection()
       paths = check_intersection()
       if paths[0]:
          # path to the left is open
          bot.turn(-90)
      elif paths[1]:
          # path forward is open - do nothing, no need to turn
          pass
      elif paths[2]:
          bot.turn(90)

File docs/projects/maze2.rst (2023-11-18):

Maze runner: pledge algorithm
============================
This is a modified version of wall following that's able to jump between islands, to solve mazes that wall following cannot.
It's a guaranteed way to reach an exit on the outer edge of any 2D maze from any point in the middle.
However, it is not guaranteed to visit every passage inside the maze, so this algorithm will not help you if you are
looking for a hidden treasure inside the maze.

Start by picking a direction, and always move in that direction when possible. When you hit a wall, start wall following,
using the left hand rule. When wall following, count the number of turns you make, a left turn is -1 and a right turn is 1.
Continue wall following until your chosen direction is available again and the total number of turns you've made is 0; then
stop following the wall and go in the chosen direction until you hit a wall. Repeat until you find an exit.

Note: if your chosen direction is available but the total number of turns is not zero (i.e. if you’ve
turned around 360 degrees or more), keep wall following until you untwist yourself. Note that Pledge
algorithm may make you visit a passage or the start more than once, although subsequent times will
always be with different turn totals.

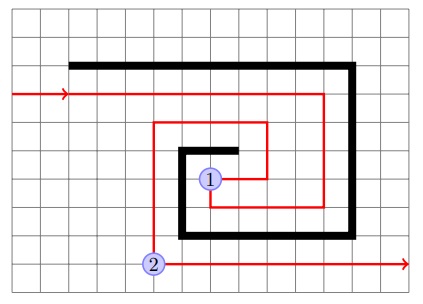
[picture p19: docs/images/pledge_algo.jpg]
Front view


In the figure above, thick black lines show the walls of the maze; the red line shows the path of the robot. At point
1, the robot turns so that it is again heading the same direction as in the beginning; however, the
number of turns at this point is not zero, so the robot continues following the wall. At point 2, the
robot is again heading in the original direction, and the number of turns is zero, so it stops following
the wall. Had the robot left the wall at point 1, it would be running in circles.

To program the Pledge algorithm, we need to keep track of robot direction and number of turns. In
fact, just the number of turns is sufficient: if we know the number of turns, we can determine
the direction. Thus, we introduce a global variable ``numTurns``. Every time we turn 90 degrees clockwise,
``numTurns`` is increased by 1; every time we turn 90 degrees counterclockwise, we decrease ``numTurns``
by 1.

Thus, the draft of the program would be

.. code-block:: python
		
	numTurns = 0
	def loop():
	    goToWall()
	    followWall()

where
	    
* Function ``gotoWall()`` goes forward along the line, through intersections, until the robot hits a wall

* Function ``followWall()`` follows the wall using left hand rule until we are again facing the same direction as before, with numTurns=0.

For each of these functions, we need to describe carefully what conditions the function expects at the start and in what condition it leaves the robot at the end (which way is it facing? is it at intersection?).

goToWall():
	* Initial condition: robot is on the line (i.e., the line is under the center of the front sensor array; robot could be at intersection), ``numTurns=0``
	* Final state: robot is at an intersection, there is a wall ahead (i.e., no passage forward), and ``numTurns=0``

followWall():
	* Initial condition: robot is at an intersection, there is a wall ahead (i.e., no passage forward), and ``numTurns=0``
	* Final state: robot is on the line (i.e., the line is under the sensor of the front sensor array; robot could be at intersection), ``numTurns=0``

When we think about implementing the algorithm, we see that in the very beginning of ``followWall()``,
the robot needs to turn so that the wall is on its left. Normally it would be just a 90 degree right
turn; however, if we are at a dead end, we need to turn 180 degrees. Thus, we need to know
whether there is a passage to the right. Therefore, we add one more condition to the final state of ``goToWall()``:

* Final state: robot is at the intersection, there is a wall ahead (i.e., no passage forward), ``numTurns=0``, and global variable ``passageRight`` contains information about whether there is a passage to the right.

To implement these two functions, we will make use of the functions ``goToIntersection()``,
``checkIntersection()`` which we used for the wall-following algorithm. 
Implementing ``goToWall()`` is trivial.

For followWall(), in the beginning we must put

.. code-block:: python

	if passageRight:
	    turn(90)
	    numTurns += 1
	else:
	    # no passage to the right - need to turn 180
	    turn(180) 
            numTurns += 2

After this, we do the regular line following algorithm: go to intersection, check intersection, turn
as needed, except that we should exit the function if, after a “turn as needed”, we have ``numTurns=0``.
We leave it to you to complete the algorithm.

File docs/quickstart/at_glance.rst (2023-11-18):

Yozh at a glance
================

The photos below show main features of Yozh:

Front view

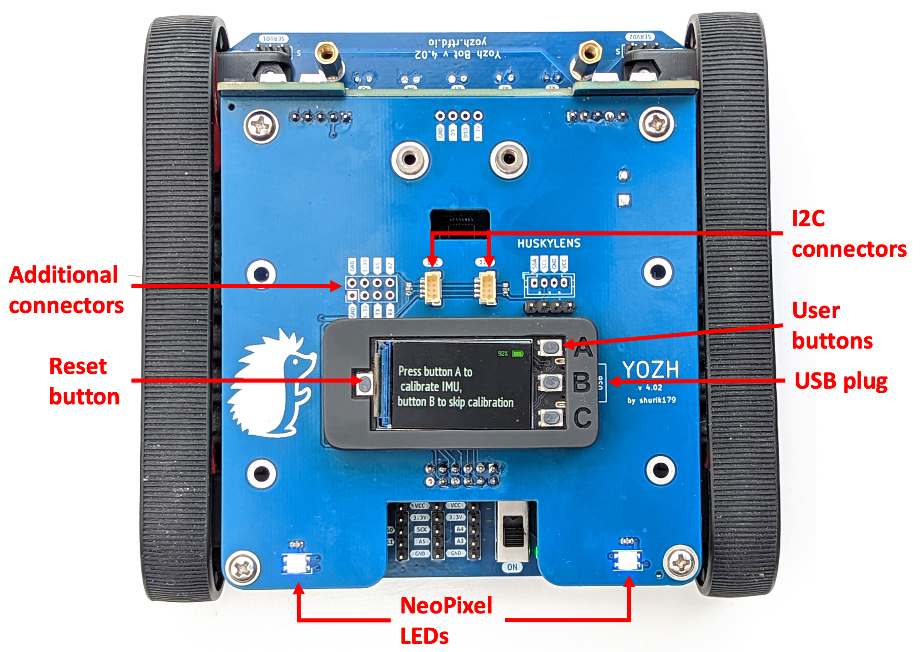
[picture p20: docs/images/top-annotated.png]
Top view


Rear view

Reflectance array

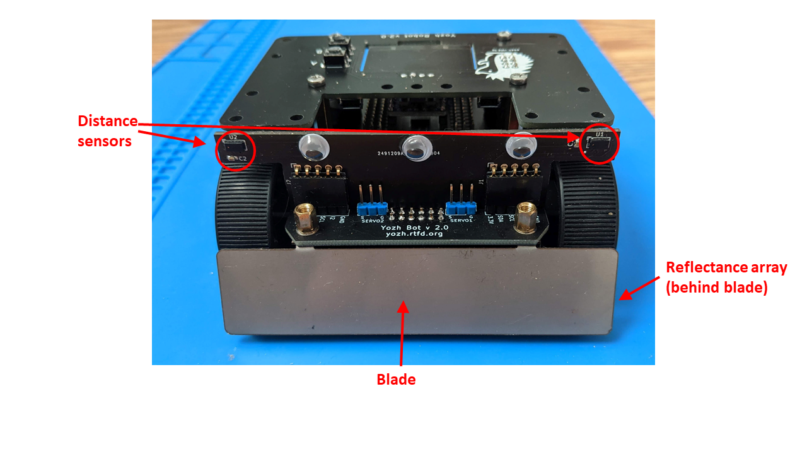
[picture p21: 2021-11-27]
docs/images/overview-front.png

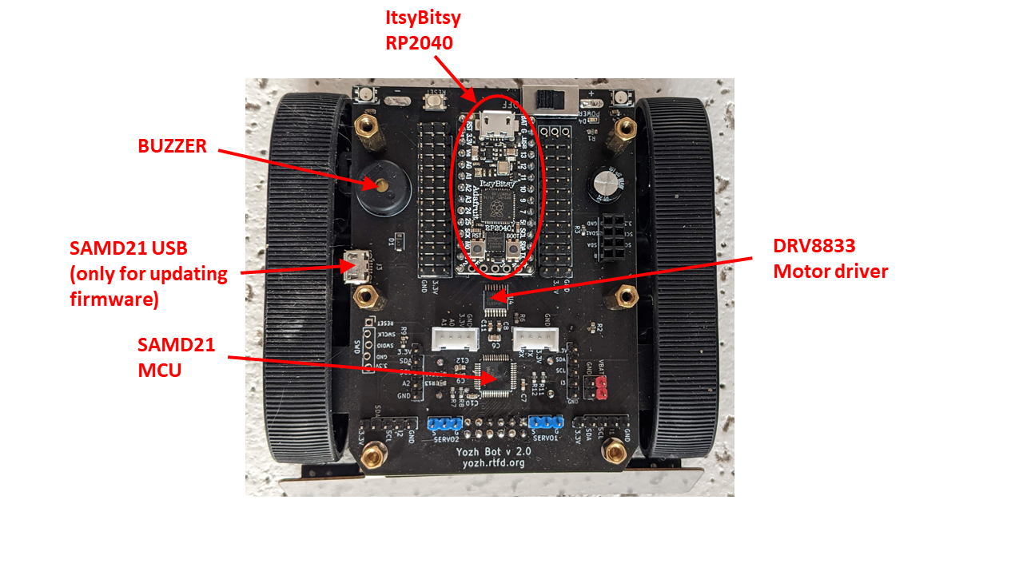
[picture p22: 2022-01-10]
docs/images/electronics.png

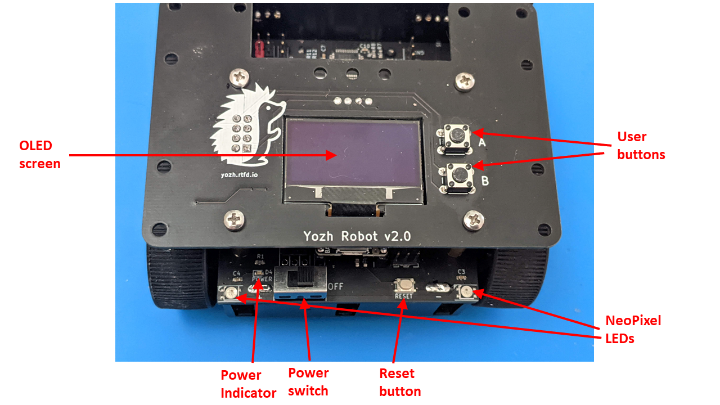
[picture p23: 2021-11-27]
docs/images/overview-back.png

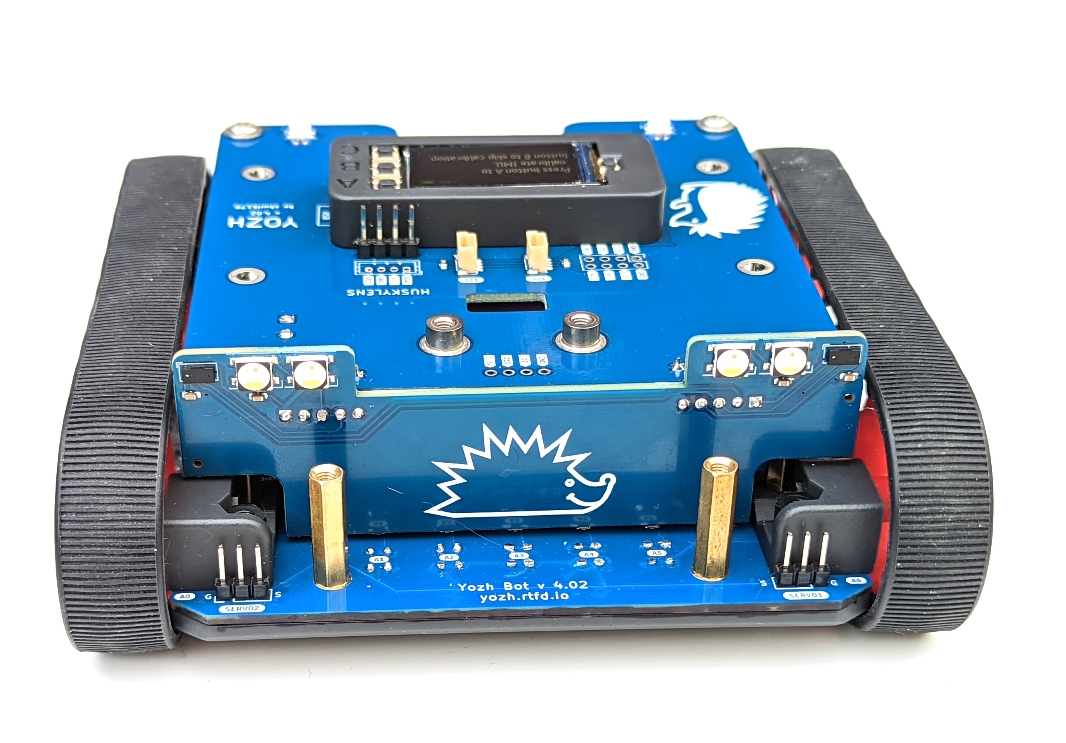
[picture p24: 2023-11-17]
docs/images/front-4.0.2.jpg

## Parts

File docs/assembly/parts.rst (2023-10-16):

Parts and materials
===================

To build Yozh Robot, you will need the following parts and materials:

* `Zumo chassis <https://www.pololu.com/product/1418>`__ by Pololu
* Two 6V N20 size micro gear motors with extended shafts. We recommend
  `these motors <https://www.pololu.com/product/2215>`__ from Pololu
* Magnetic `encoder disk <https://www.pololu.com/product/2599>`__ fitting on
  the extended shaft of the motor. (You only need two, but Pololu sells them in
  packs of 5). Note that you do not need to buy encoders, only the disks -
  encoder sensors are built into the main Yozh board.
* Yozh robot kit, available from Tindie (SOON - link coming). Contents of this kit,
  together with alternatives for those who
  prefer to build your own, is described below.
* Four AA batteries. Usual alkaline batteries will work but won't last long,  
  so use of  heavy-duty NiMH rechargeable batteries such as
  `Panasonic Eneloop Pro <https://www.amazon.com/Panasonic-BK-3HCCA4BA-eneloop-Pre-Charged-Rechargeable/dp/B00JHKSL28/>`__
  is strongly recommended. You will also need a charger for these batteries.

Yozh kit contents
-----------------
Below is the contents of the Yozh kit, together with alternative sources
for buying these parts if for some reason you prefer not to use the kit.

*  Itsy Bitsy RP2040 microcontroller (available from `Adafruit <https://www.adafruit.com/product/4888>`__)
   and male headers

* Five custom PCBs:

  * Main electronics board
  * Spacer board
  * Reflectance sensor array board
  * Top cover with OLED display
  * Front distance sensor board
  Design files and BOM for these boards are available from Yozh |github|.

* Steel front blade to be attached to the robot. The blade is made of  0.030" stainless
  steel; DXF file for the blade is in |github|. You can use Pololu's `lasercutting
  services <https://www.pololu.com/product/749>`__ to cut the blade for you.

* Mounting hardware:

  * Four 22mm M2.5 female brass standoffs and 8 M2.5 screws (8mm length), for mounting
    the top plate
  * Two 15mm M3 brass female standoffs and two M3 screws, for attaching the
    reflectance sensor board
  * Two 6mm M3 M-F standoffs. Note: it is required that the male thread length be at
    least 6mm, which is somewhat unusual. You can find such standoffs on AliExpress,
    e.g. here: https://www.aliexpress.com/item/32872847199.html?spm=a2g0s.9042311.0.0.27424c4dmfu9xI
    (choose option **M3 (thread 8mm)**, and length 6mm).

* Two long (15mm) 4-pin male headers

Tools
-----
You will also need to have a computer to program the robot, and some basic tools:
soldering iron, wire strippers, flush cutters, screwdriver, pliers.

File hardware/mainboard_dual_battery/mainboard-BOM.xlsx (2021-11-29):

Component | Description | Part Number | References | Value | Footprint | Quantity Per PCB | Side | Datasheet | LCSC | Comment
1 | SMD capacitor, 0603, 10nF |  | C11 | 10nF | C_0603_1608Metric | 1 | Top | ~ | C57112
2 | SMD capacitor, 0603, 100nF |  | C3 C4 C7 C9 C10 C15 | 100nF | C_0603_1608Metric | 6 | Top | ~ | C14663
3 | SMD capacitor, 0603, 100nF |  | C13 C14 | 100nF | C_0603_1608Metric | 2 | Bottom | ~ | C14663
4 | SMD capacitor, 0603, 1uF |  | C1 C2 C12 | 1uF | C_0603_1608Metric | 3 | Top | ~ | C15849
5 | SMD capacitor, 0603, 2.2uF |  | C8 | 2.2uF | C_0603_1608Metric | 1 | Top | ~ | C23630
6 | SMD capacitor, 0603, 10uF |  | C6 | 10uF | C_0805_2012Metric | 1 | Top | ~ | C15850
7 | Electrolytic capacitor, 220uF, 8*7 |  | C5 | 220uF | C_Radial_D8.0mm_H7.0mm_P3.50mm | 1 | Top | ~ | C45072
8 | LED, Green, 0603 | LED | D4 | LED | LED_0603_1608Metric | 1 | Top | ~ | C72043
9 | RGB LED with integrated controller, 3.5mm | SK6812MINI | D2 D3 | SK6812MINI | LED_SK6812MINI_PLCC4_3.5x3.5mm_P1.75mm | 2 | Top | https://cdn-shop.adafruit.com/product-files/2686/SK6812MINI_REV.01-1-2.pdf
10 | 1000V 1A General Purpose Rectifier Diode, MELF | SM4007 | D1 | SM4007PL | D_SOD-123F | 1 | Top | http://cdn-reichelt.de/documents/datenblatt/A400/SMD1N400%23DIO.pdf | C64898
11 | USB Micro Type B connector | 10118194-0001LF | J3 |  | USB_Micro-B_Amphenol_10118194_Horizontal | 1 | Top | ~ | C132563
12 | SMD resistor, 0603, 1K |  | R9 R10 | 1K | R_0603_1608Metric | 3 | Top | ~ | C21190
13 | SMD resistor, 0603, 2.2K |  | R1 R2 R3 R4 R5 | 2.2K | R_0603_1608Metric | 4 | Top | ~ | C4190
14 | SMD resistor, 0603, 10K |  | R6 R7 R8 R11 R12 R13 R14 | 10K | R_0603_1608Metric | 7 | Top | ~ | C25804
15 | Tactile switch | K2-1808SN-A4SW-01 | SW2 |  | SW_SPST_HRO-K2-1808SN | 1 | Top | ~ | C92589
16 | Switch, SPDT | SS-12D10L3 | SW1 |  | SW_XKB_SS12D10L3 | 1 | Top | ~ | C319013
17 | SAM D21 Microchip SMART ARM-based Flash MCU, 48Mhz, 256K Flash, 32K SRAM, TQFP-48 | ATSAMD21G18A-AU | U5 | ATSAMD21G18A-AU | QFP-48_7x7_Pitch0.5mm_reduced | 1 | Top | http://ww1.microchip.com/downloads/en/DeviceDoc/SAM_D21_DA1_Family_Data%20Sheet_DS40001882E.pdf | C78624
18 | 1A 20V Fixed LDO Linear Regulator, 3.3V, SOT-89/SOT-223/TO-220/TO-252/TO-263 | AZ1117EH-3.3 | U1 | AZ1117EH-3.3TRG1 | SOT-223 | 1 | Top | https://www.diodes.com/assets/Datasheets/AZ1117.pdf | C108494
19 | Dual H-Bridge Motor Driver, HTSSOP-16 | DRV8833PWP | U4 | DRV8833PWP | HTSSOP-16-1EP_4.4x5mm_P0.65mm_EP3.4x5mm_Mask2.46x2.31mm_ThermalVias_reduced | 1 | Top | http://www.ti.com/lit/ds/symlink/drv8833.pdf | C50506
20 | Dual -Channel, High-Sensitivity, Hall-Effect Latch,SOT23-5 | TMAG5111C2AQDBVR | U2 U3 | TMAG511x | SOT-23-5 | 2 | Bottom | https://www.ti.com/lit/ds/symlink/tmag5111.pdf
21 | Buzzer | PS1240P02BT | BZ1 |  | Buzzer_TDK_PS1240P02BT_D12.2mm_H6.5mm | 1 | Top | ~ | C76871
22 | Male header, 3p, 0.1" |  | J18 J19 |  | PinHeader_1x03_P2.54mm_Vertical | 2 | Top | ~
23 | Grove connector |  | J7 J8 |  | PinHeader_1x04_P2.0mm_Vertical | 2 | Top | ~
24 | Male header, 5p, 0.1" |  | J5 J6 J20 J21 |  | PinHeader_1x05_P2.54mm_Vertical | 4 | Top | ~
25 | Male header, 14p, 0.1" |  | J1 J4 J9 J13 J14 J15 |  | PinHeader_1x14_P2.54mm_Vertical | 6 | Top | ~
26 | Female header, 14p, 0.1" |  | J10 J11 |  | PinSocket_1x14_P2.54mm_Vertical | 2 | Top | ~ | C52711
27 | Male header, 2*4p, 0.1" |  | J25 |  | PinHeader_2x02_P2.54mm_Vertical | 1 | Top | ~
28 | Female header, 2*4p, 0.1" |  | J26 |  | PinSocket_2x04_P2.54mm_Vertical | 1 | Top | ~ | C92271
29 | Female header, 2*6p, 0.1" |  | J12 |  | PinSocket_2x06_P2.54mm_Vertical | 1 | Bottom | ~ | C92269

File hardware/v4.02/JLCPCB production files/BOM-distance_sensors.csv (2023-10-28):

Comment | Designator | Footprint | LCSC
100nF | C1,C2,C3,C4 | C_0603_1608Metric | C14663
SK6812 | D1,D2,D3,D4 | LED_SK6812_PLCC4_5.0x5.0mm_P3.2mm | C5380878
VL53L0X | U1,U2 | ST_VL53L1x | C91199

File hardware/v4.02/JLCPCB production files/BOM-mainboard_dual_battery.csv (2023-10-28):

Comment | Designator | Footprint | LCSC
USB_B_Micro | J3 | USB_Micro-B_Amphenol_10118194_Horizontal | C132563
100nF | C10,C11,C12,C13,C18,C27,C6 | C_0603_1608Metric | C14663
1uF | C16,C17,C8 | C_0603_1608Metric | C15849
10uF | C2,C3,C5 | C_0805_2012Metric | C15850
2.2nF | C25 | C_0603_1608Metric | C1604
76.8k | R18 | R_0603_1608Metric | C165743
47pF | C26 | C_0603_1608Metric | C1671
icm42688 | U12 | Bosch_LGA-14_3x2.5mm_P0.5mm | C1850418
1K | R21 | R_0603_1608Metric | C21190
SS54 | D3 | D_SMA | C22452
1R | R22 | R_0603_1608Metric | C22936
51k | R20 | R_0603_1608Metric | C23196
2.2uF | C7,C9 | C_0603_1608Metric | C23630
SSW32768KF3CHC-IT | X1 | Crystal_SMD_3225-4Pin_3.2x2.5mm_small_pads | C253931
10K | R1,R12,R13,R14,R16,R17,R2,R3,R4,R5,R6,R7 | R_0603_1608Metric | C25804
22uH | L1 | L_Taiyo-Yuden_NR-40xx | C2880384
330uF | C19,C4 | CP_Elec_6.3x7.7 | C2980164
SW_SPDT_XKB_SSD1210L3 | SW1 | SW_XKB_SS12D10L3 | C319013
10 | R15 | R_0603_1608Metric | C319921
4.7uH | L2 | L_Panasonic-ETQP3M | C412309
20k | R19 | R_0603_1608Metric | C4184
2.2K | R10,R11,R8,R9 | R_0603_1608Metric | C4190
AP3019A | U10 | TSOT-23-6 | C44956
22uF | C1,C20,C21,C22 | C_0805_2012Metric | C45783
Conn_01x05 | J10,J2,J9 | PinHeader_1x05_P2.54mm_Vertical | C492404
Conn_01x03 | J11,J12 | PinHeader_1x03_P2.54mm_Vertical | C49257
DRV8833PWP | U11 | HTSSOP-16-1EP_4.4x5mm_P0.65mm_EP3.4x5mm_Mask2.46x2.31mm_ThermalVias_reduced | C50506
AP2112K-3.3 | U1 | SOT-23-5 | C51118
ITR9909 | U2,U3,U4,U5,U6,U7,U8 | Everlight_ITR9909 | C53399
Conn_02x06_Odd_Even | J13 | PinSocket_2x06_P2.54mm_Vertical | C541855
10nF | C14,C15,C23,C24 | C_0603_1608Metric | C57112
Battery_Cell | BT1 | BatteryHolder_MYOUNG_BH-18650-B1BA007_2x18650 | C6937126
LED | D1,D2 | LED_0603_1608Metric | C72043
PAM2423 | U14 | SOIC-8-1EP_3.9x4.9mm_P1.27mm_EP2.62x3.51mm | C781891
ATSAMD21G18A-A | U15 | QFP-48_7x7_Pitch0.5mm_reduced | C78624

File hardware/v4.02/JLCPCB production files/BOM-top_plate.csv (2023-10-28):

Comment | Designator | Footprint | LCSC
100nF | C1,C2 | C_0603_1608Metric | C14663
Conn_01x04 | J8,J9 | JST_SH_BM04B-SRSS-TB_1x04-1MP_P1.00mm_Vertical | C160390
3.3K | R1,R2 | R_0603_1608Metric | C22978
Conn_01x04 | J7 | connector-4p-generic-nosilk | C2691448
SK6812MINI | D1,D2 | LED_SK6812MINI_PLCC4_3.5x3.5mm_P1.75mm | C2886570
SMTSO3035 | M1,M2 | mounting_SMD_NUT_M3_H6mm | C2916333

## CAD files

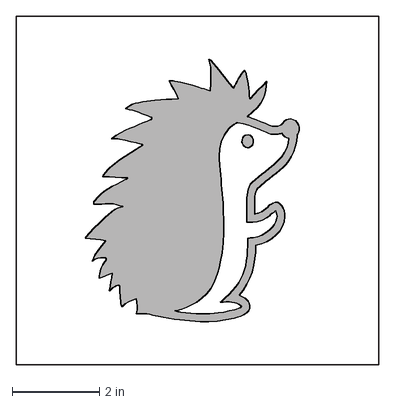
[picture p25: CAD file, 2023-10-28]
docs/images/logo/headgehog.dxf
8.28 x 7.96 in

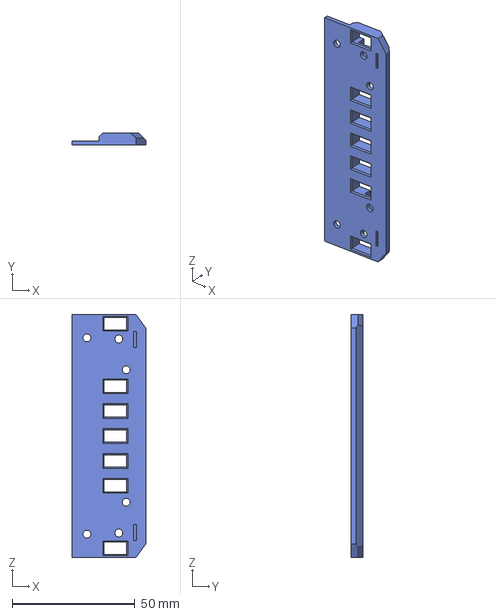
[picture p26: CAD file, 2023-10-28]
hardware/v4.02/3d printed/bottom_front_spacer_4.02.step
30.0 x 5.00 x 99.0 mm

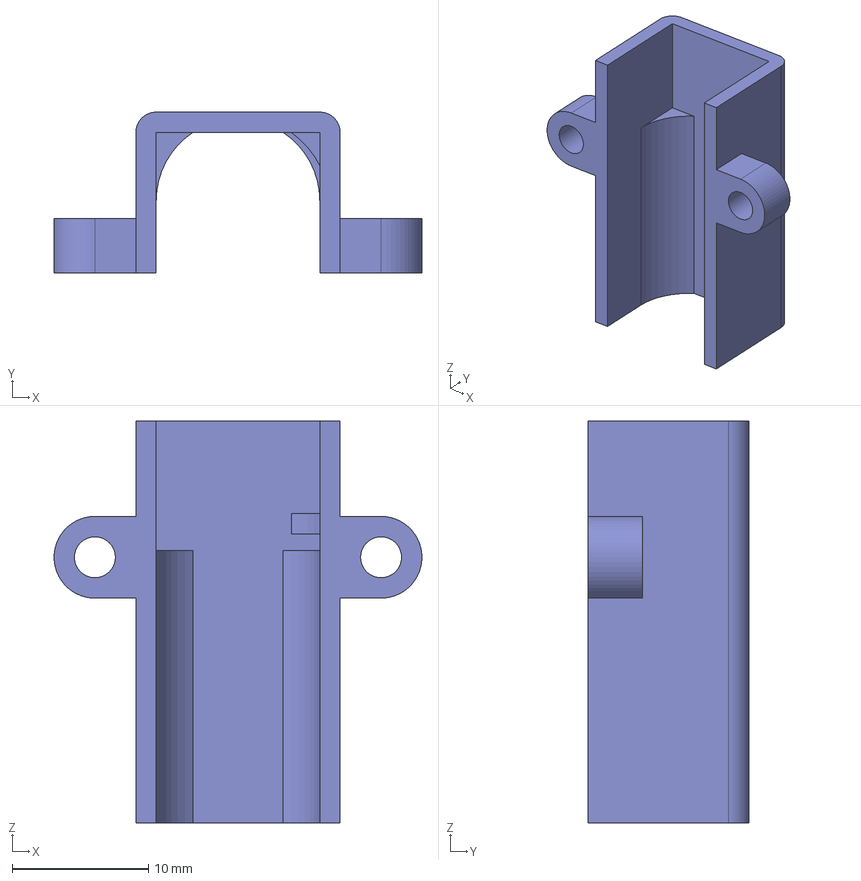
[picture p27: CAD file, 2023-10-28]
hardware/v4.02/3d printed/motor_bracket_4.02.step
27.0 x 11.8 x 29.5 mm

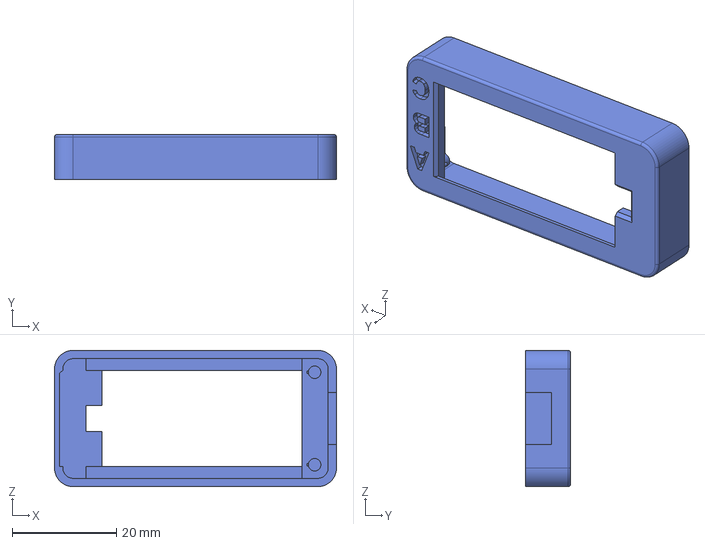
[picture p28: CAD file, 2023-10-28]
hardware/v4.02/3d printed/Feather_cover_4.02.step
54.2 x 8.70 x 26.2 mm

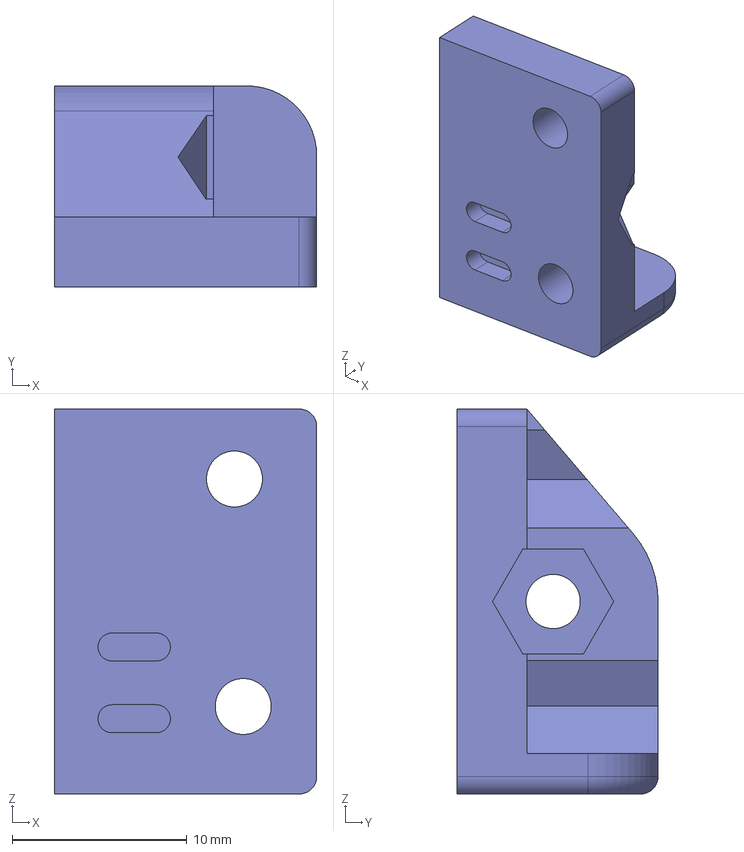
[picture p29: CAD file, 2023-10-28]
hardware/v4.02/3d printed/Wheel support mirror 4.02.step
15.0 x 11.5 x 22.0 mm

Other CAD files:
hardware/v4.02/3d printed/bottom_front_spacer_4.02 v2.stl
hardware/v4.02/3d printed/Wheel support 4.02.step
hardware/v4.02/3d printed/Feather_cover_4.02.stl
hardware/v4.02/3d printed/Wheel support 4.02.stl
hardware/v4.02/3d printed/Wheel support mirror 4.02.stl
hardware/v4.02/3d printed/motor_bracket_4.02.stl

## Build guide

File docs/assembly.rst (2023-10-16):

.. _assembly:
********************
Yozh Assembly Guide
********************
This document describes the assembly of Yozh robot.

.. toctree::
    :caption: Table of Contents
    :maxdepth: 1

    assembly/parts
    assembly/motors
    assembly/chassis
    assembly/chassis_solder
    assembly/reflectance
    assembly/top
    assembly/final

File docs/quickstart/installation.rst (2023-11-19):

Circuit Python library  installation
====================================
Yozh is intended to be programmed in CircuitPython 8 - an implementation of
Python programming language for microcontrollers, created by Adafruit (based on
Micropython, another Python implementation). For general background on Circuit
Python, please visit `What is CircuitPython? <https://learn.adafruit.com/welcome-to-circuitpython/what-is-circuitpython>`__
page.

CircuitPython must already be installed on the ESP32-S3 microcontroller
serving as the brains of Yozh Robot. If not, please do so now
following `Adafruit's  instructions <https://learn.adafruit.com/esp32-s3-reverse-tft-feather/install-circuitpython>`__.

Next, you need to install Yozh Circuit Python library. Go to |github| and click
on green ``Code`` button to download the zip file containing all Yozh designs
and software.  Extract the zip file to your computer. Find in the extracted archive folder 
`circuitpython_library` 

Connect Yozh robot to the computer using a  USB-C cable.  It should appear in
your file browser as an external drive with the name `CIRCUITPY`. Open it to
view contents. 
Now, copy the following files and folders from the downloaded `circuitpython_library` folder to the 
`CIRCUITPY` folder: 

* `yozh.py`
* `yozh_registers.py`
* `hedgehog.bmp`
* `fonts` folder 
* `lib` folder (`CIRCUITPY` may already contain folder `lib`; if so, copy 
  all contents of `circuitpython_library/lib` to `CIRCUITPY/lib`)

if you intend to use Yozh with Huskylens camera by DFrobot, you also need to copy file `huskylens.py`.  

Please note that extracted Yozh  archive also contains a folder `circuitpython_library/examples`.
Move this folder to some convenient location on your computer - you will use it shortly.

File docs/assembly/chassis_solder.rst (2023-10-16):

Soldering the chassis
=====================

Before continuing, make sure that power switch on the main board is in **OFF**
position.

Using the soldering iron, solder the motor leads protruding through the main
board to the board. Be careful with nearby  connectors - try to avoid touching
them with your iron. Use flush  cutters to trim remaining length of motor leads.

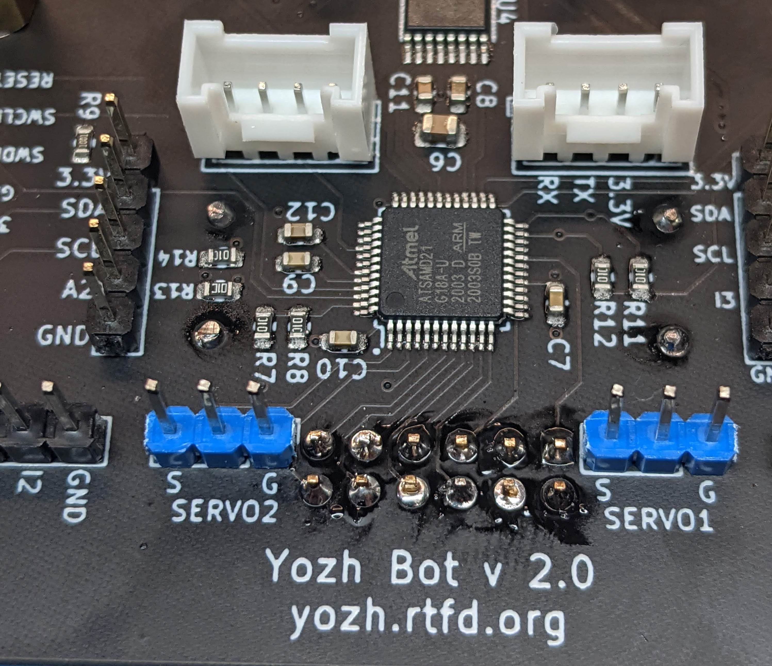
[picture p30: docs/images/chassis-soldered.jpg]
Chassis with soldered motor leads


Now, turn the chassis over and insert the  two individual battery contacts as
shown in ` this drawing <https://a.pololu-files.com/picture/0J9740.1200.png>`__
by Pololu.  The solder tabs of the
two individual contacts should go through the holes in battery compartment and
into the slots in the spacer board and the main board.

Insert 4 AA batteries
(making sure they are in correct polarity) to hold the battery terminals in
place until you solder them and close the  battery compartment cover.   Turn the chassis
over again and inspect the battery terminals; the top of solder tab should be
level with the top of the main board. If necessary, adjust the battery terminals.

Solder the tabs of the battery contacts to the  main board. The easiest way to
do that is by using a larger iron tip, heating the plating of the slot in the
main board, and then filling it with solder.

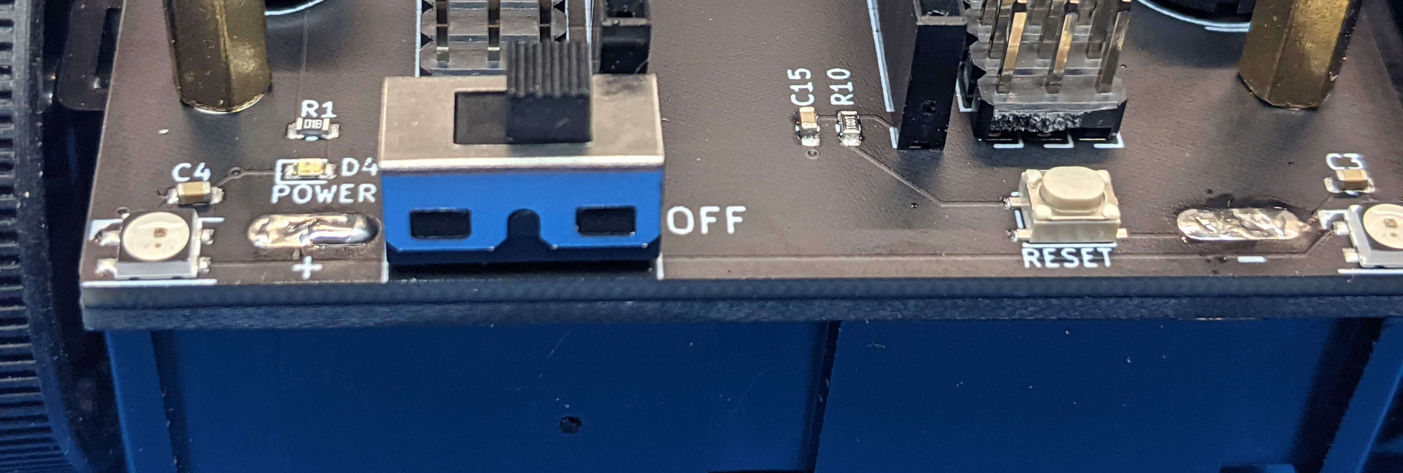
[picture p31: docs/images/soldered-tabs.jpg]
Chassis with soldered battery tabs


Once the solder cools, turn the switch on. The LEDs on the robot should light up,
indicating that the robot is powered.

Turn the robot off again.

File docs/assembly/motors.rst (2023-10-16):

Preparing motors
================

Prepare  four pieces of solid core 22AWG wire. Each piece needs to be about
5cm long, about half of which should be stripped. (It is easiest to first strip
2.5cm from a roll of wire and then cut.) Use pliers
to form a short (about 3mm) 90 degree bend at **one** end of each of these pieces
of wire, as shown in the photo below.

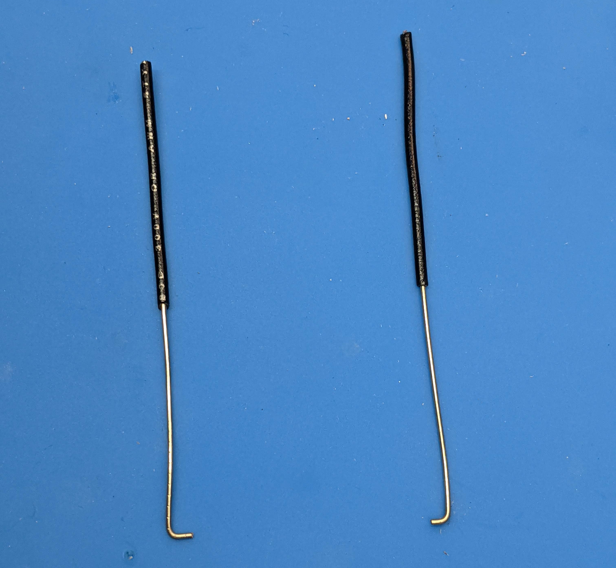
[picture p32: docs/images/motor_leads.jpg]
Motor leads


Now, take the motors. Attach the sprocket to each motor, paying attention to
orientation: the side of the sprocket with the "lip" should be facing outwards.

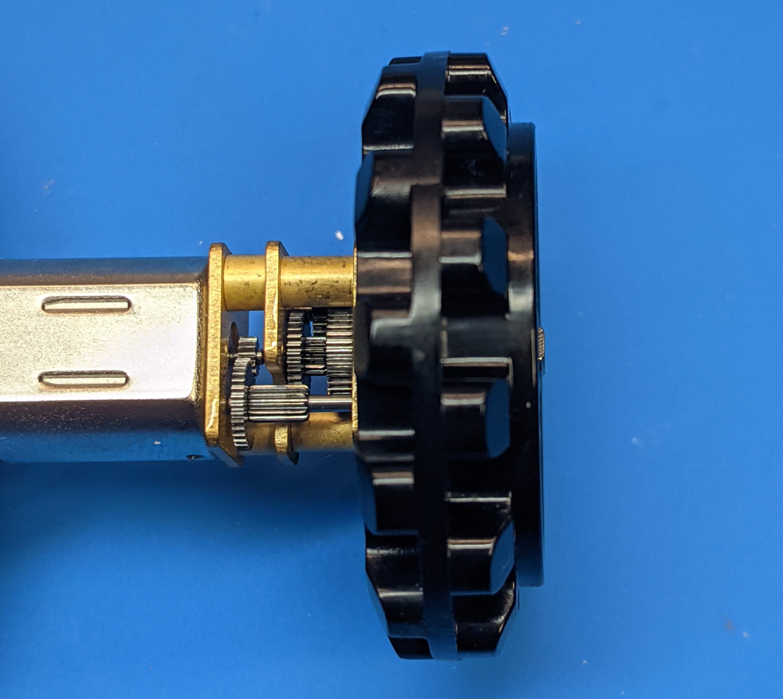
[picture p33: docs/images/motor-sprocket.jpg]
Motor with sprocket


Place the motors on the table, using sprockets as supports, and solder the motor
leads to each motor. (You probably want to use a third hand or similar device
to support the wires while soldering. )

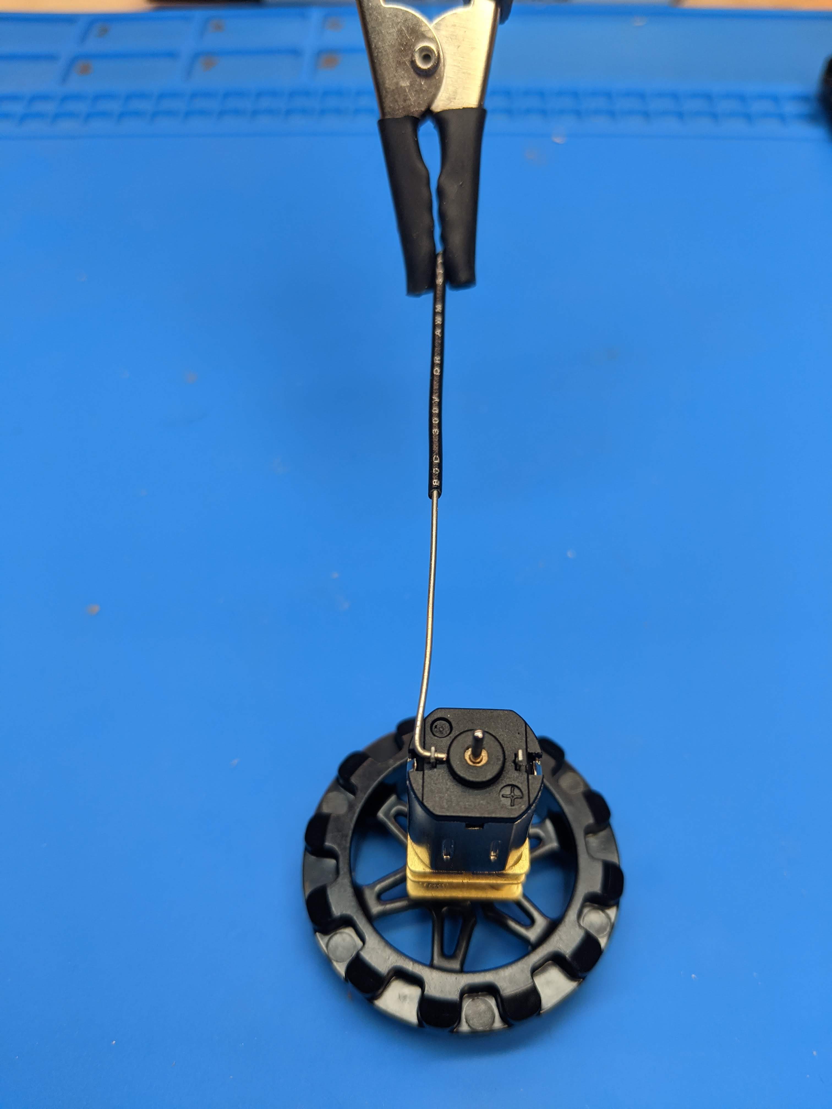
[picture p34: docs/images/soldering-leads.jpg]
Soldering motor leads


**Important**: pay attention to proper orientation of the motors! One of motor
terminals is marked +; make sure that this terminal is on the right side as
shown in the photos.

After soldering the leads, cut off the unstripped part of each motor lead - it was
only needed to make it easier to hold the wire while soldering.

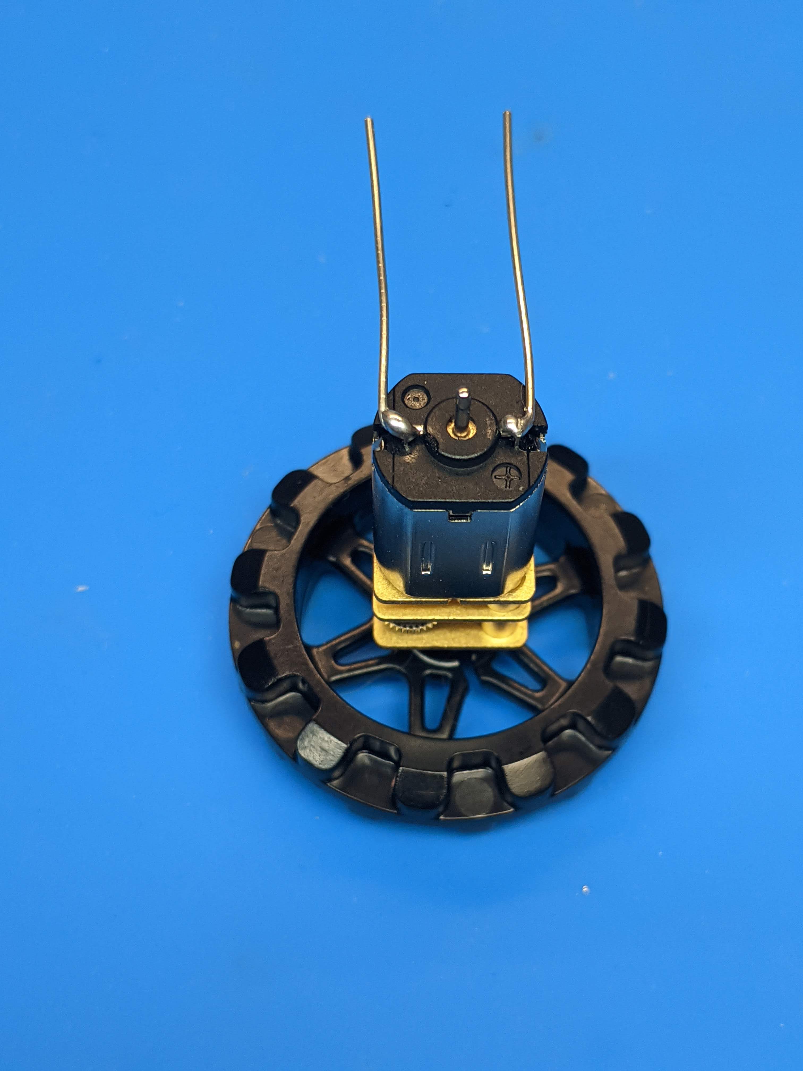
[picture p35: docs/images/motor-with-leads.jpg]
Motor with leads soldered


Finally, put the magnetic encoder disks on the rear shafts of the motors.

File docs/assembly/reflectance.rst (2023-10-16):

Reflectance array and the blade
===============================
Next step is attaching the reflectance sensor array to the front of the robot.

1. Get the reflectance sensor array and inspect the pins of the soldered header.
   If they are bent, try to gently straighten them.

2. Use M3 screws to attach the two 14mm M3 standoffs to the reflectance sensor
   array as shown in the photo.

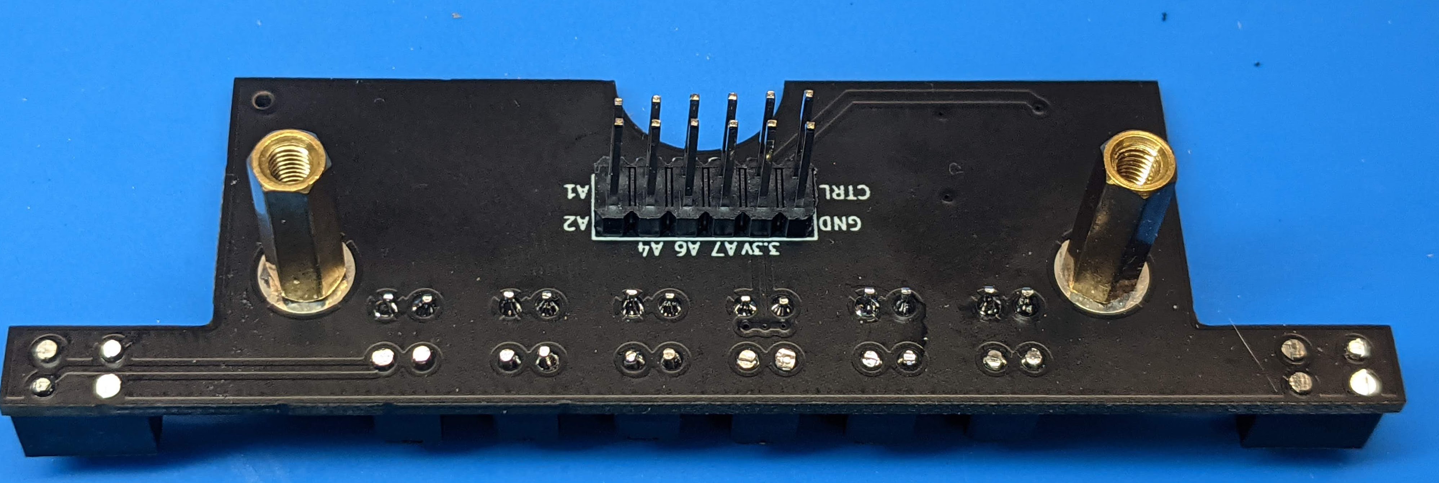
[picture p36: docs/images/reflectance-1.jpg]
Reflectance array with standoffs


3. Plug the reflectance array into the female header at the bottom of the robot
   main board. Pull it slightly out so that there is a small gap (about 1mm)
   between the top of the standoff and the bottom of the main board.

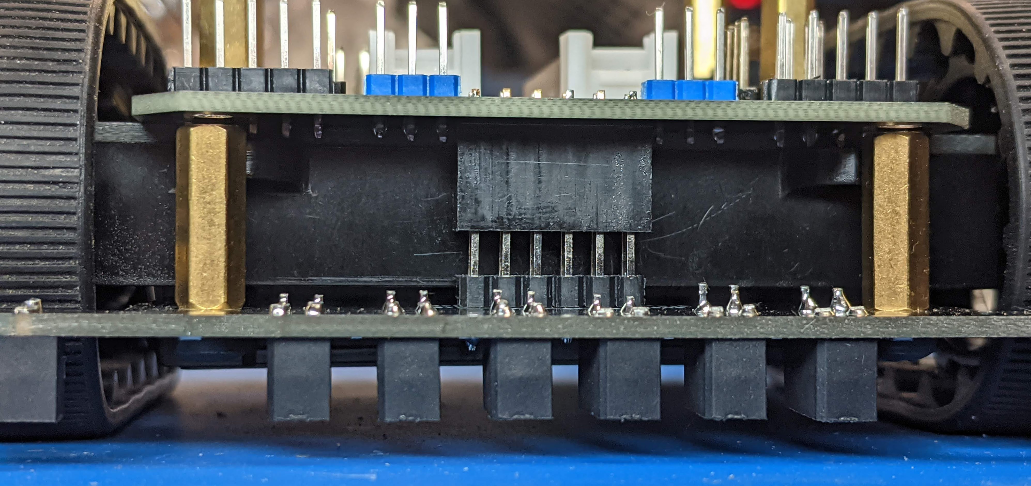
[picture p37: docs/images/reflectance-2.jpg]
Reflectance array connected to the robot


4. Get the blade. Using pliers, bend the two tabs to about 70 degree angle.

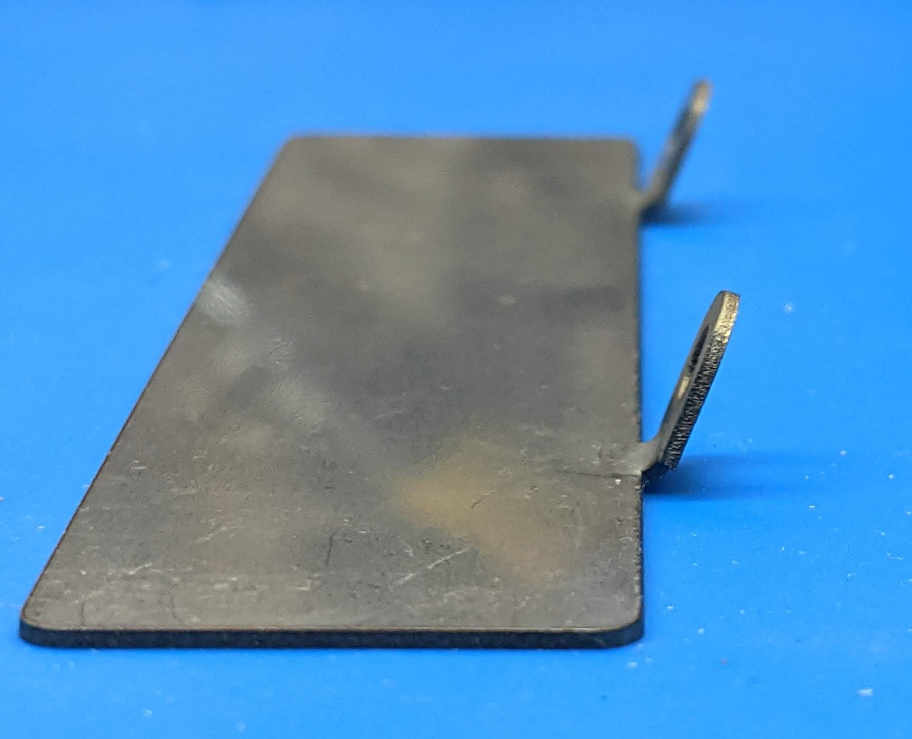
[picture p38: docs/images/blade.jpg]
Blade


5. Insert the blade so that the tabs fit in the gap between the main board and
   the standoffs. If you bent it to the correct angle, the front of the array
   will be touching the blade. If necessary, remove the blade and use pliers again
   to adjust the angle.

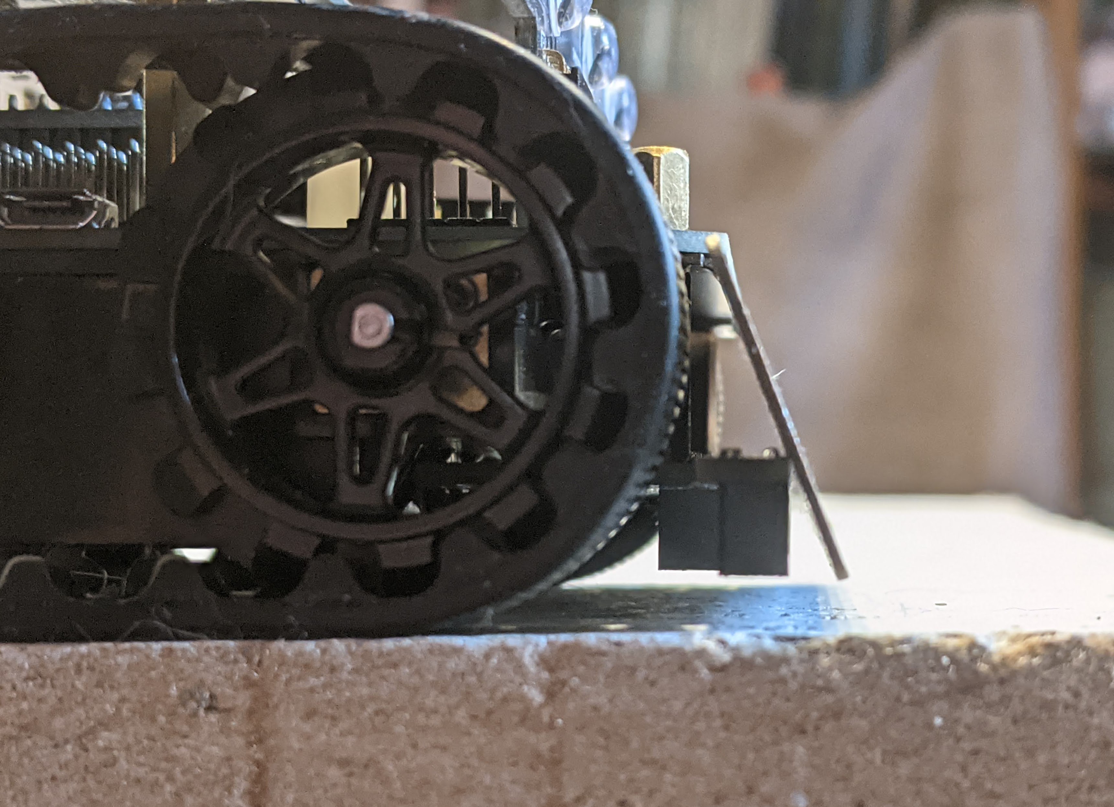
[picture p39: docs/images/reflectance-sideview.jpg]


6. Insert the short M-F M3 standoffs in the holes at the top of main board, through
   the hole in the blade tabs and into the long M3 standoff. Tighten by hand.

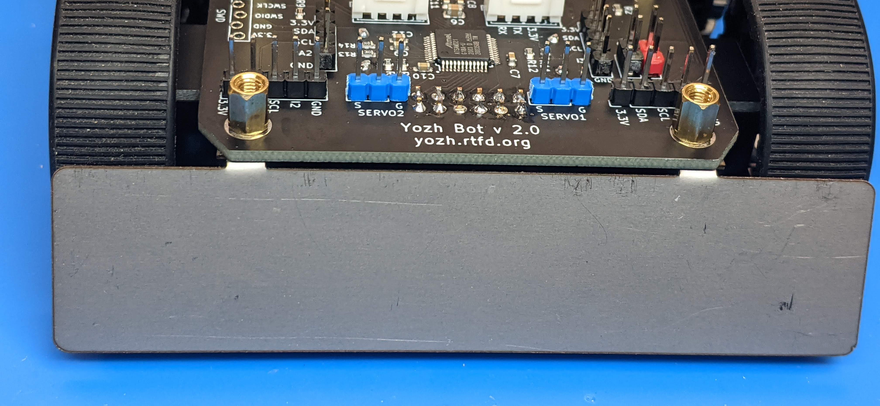
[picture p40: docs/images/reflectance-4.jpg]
Reflectance array connected to the robot


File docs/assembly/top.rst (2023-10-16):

Itsy Bitsy and the top board
============================

Before proceeding, make sure that the main switch on Yozh robot is in OFF
position.

1. Install CircuitPython 7 on your  Itsy Bitsy RP2040 microcontroller as described
   in `Adafruit Learn Guide <https://learn.adafruit.com/adafruit-itsybitsy-rp2040/circuitpython>`__.

2. Solder two 14-pin male headers to the  Itsy Bitsy board. If you need help
   with that, check `this guide <https://learn.adafruit.com/adafruit-feather-rp2040-pico/assembly>`__ -
   it is about a different board, but the process is the same, except that Itsy
   Bitsy uses two 14-pin headers. **Do not solder headers to the short edge!**

3. Insert the Itsy Bitsy board into the female headers on the main Yozh board,
   with the USB connector facing out. Double-check that it is plugged correctly -
   it is easy to make a mistake, shifting the board by one position.

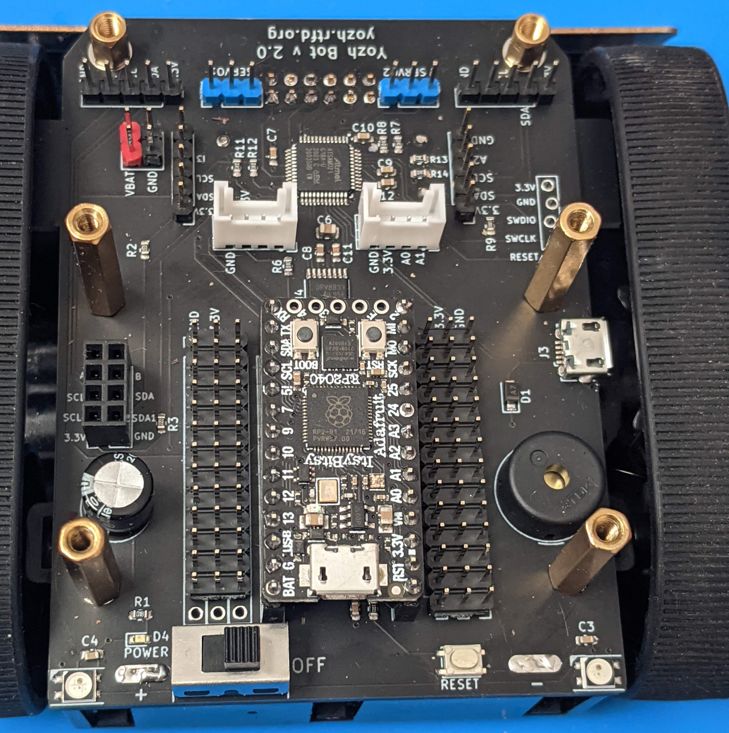
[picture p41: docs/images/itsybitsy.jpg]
ItsyBitsy installed


4. Insert the two 4-pin 15mm male headers into the 2*4 female header on the main
   Yozh board.

5. Take the top plate board, with the OLED display, and place it on top of the
   robot so that the male headers from the previous step are plugged into the 2*4
   female header on the bottom of the top plate. Double-check that it is plugged
   correctly by looking from the sides. Now double-check again.

6. Use the M2.5 screws to attach the top plate to the standoffs on the Yozh robot.

7. Plug the front distance sensor board into male headers at the front of the robot, with
   the sensors facing out.

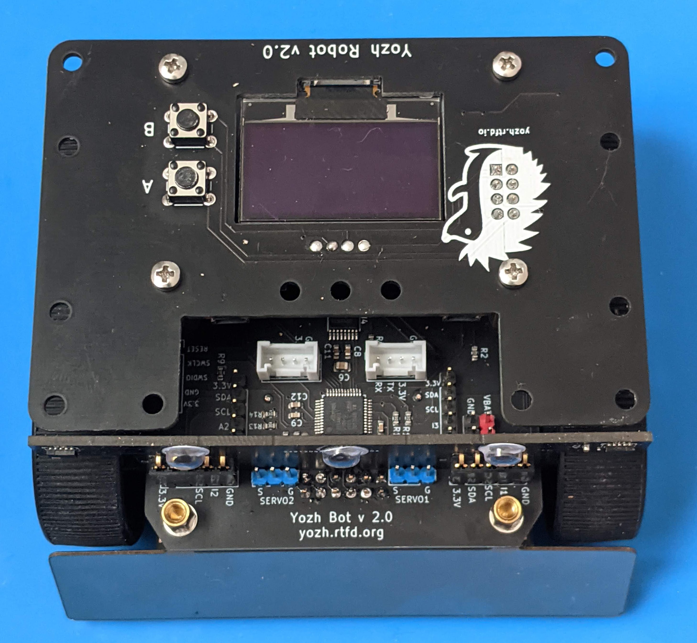
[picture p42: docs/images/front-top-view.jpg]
Robot fully assembled


8. (optional) Attach googly eyes!

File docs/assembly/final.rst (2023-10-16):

This is it!
===========
Your robot is now complete. Check the :ref:`Quickstart guide <quickstart>`   to
start  programming and using your Yozh!

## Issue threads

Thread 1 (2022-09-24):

Yozh is no longer recognized as a Drive

QuadNuker29, 2022-09-24:
Hey, this is David R from Sigma.
Before, when I would plug the robot into the computer, it would get recognized as a storage drive and pop up in files. Now it just draws power but doesn't connect. How should I fix this?
Contact me at quadnuker29@gmail.com

shurik179, 2022-09-24:
Hi, David!
Yes, we had multiple problems with CIRCUITPY drive disappearing, not sure why.
I wrote some ways to fix this in this google doc:
https://docs.google.com/document/d/1C4rf-fTO2_A6d-Higqi1a8Bx7qhjb13ecvsjiudTvfw/edit?usp=sharing
(see page 2)

shurik179, 2023-10-28:
closed

Closed 2023-10-28.

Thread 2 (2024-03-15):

Board Not Recognized

QuadNuker29, 2024-03-15:
I decided to try to experiment with the robot again after a few months, and to begin, I flashed the drive, and reinstalled the Adafruit 7.3.2 firmware using the sc2022 folder. I also reinstalled yozh.py and lib, all from the sc2022 folder.
The problem: When I try to run any program on the bot, for example basic_test.py, it throws an error:

= RESTART: E:\basic_test.py
Traceback (most recent call last):
  File "E:\basic_test.py", line 4, in <module>
    import yozh
  File "E:\yozh.py", line 32, in <module>
    import board
ModuleNotFoundError: No module named 'board'

What can I do to fix this issue and continue experimenting?

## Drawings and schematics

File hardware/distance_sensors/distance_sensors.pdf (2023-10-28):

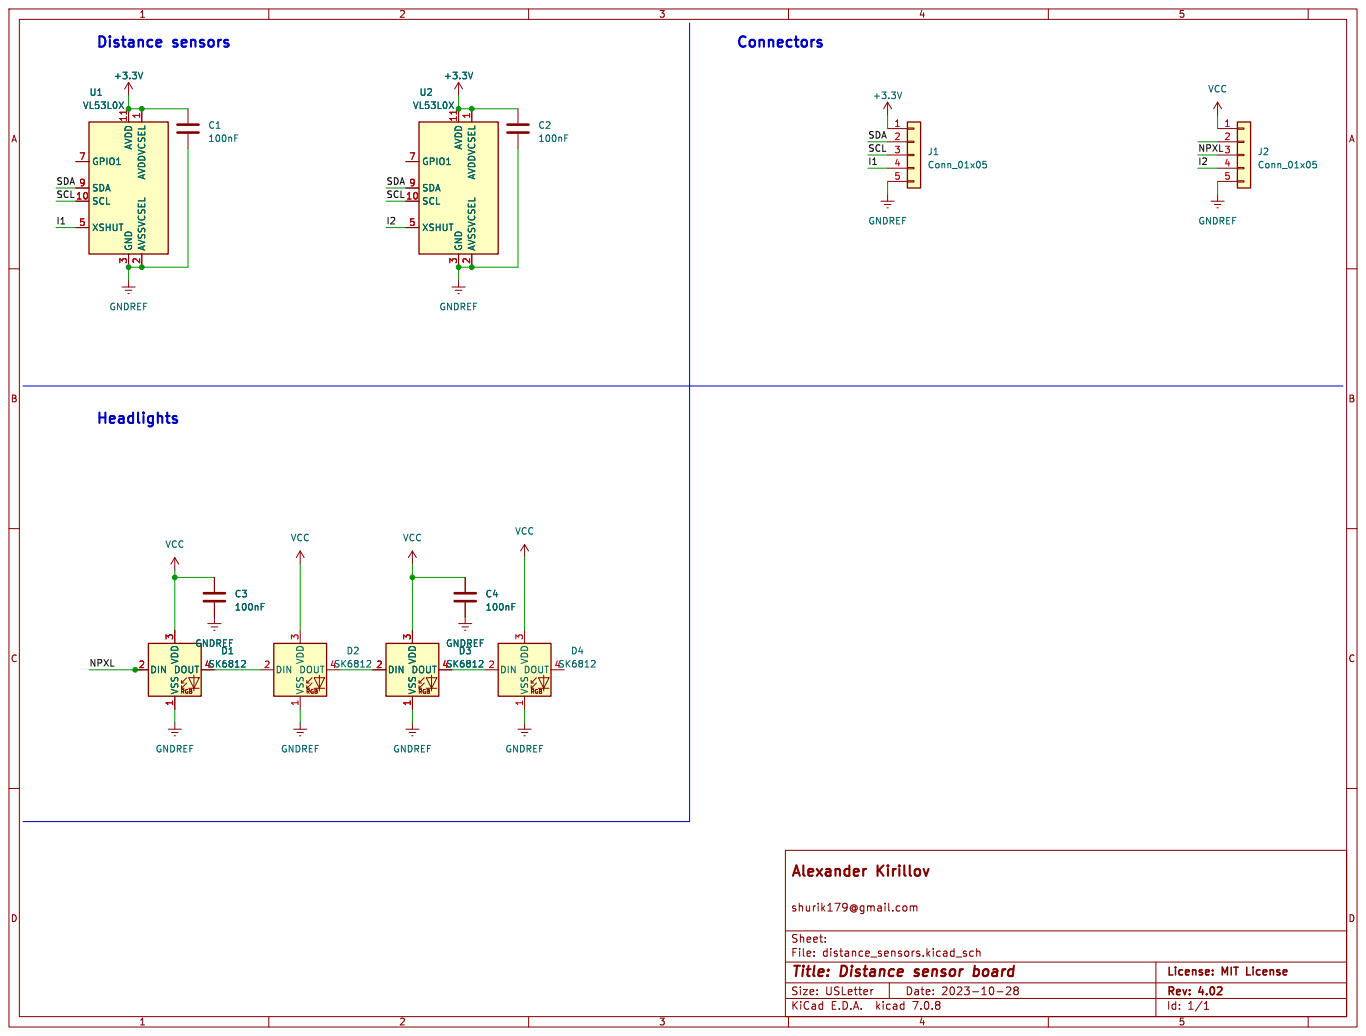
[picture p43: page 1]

3 DOUT 4 D2 SK6812 VCC GNDREF GNDREF VCC GNDREF VCC

Id: 1/1 Title: Distance sensor board

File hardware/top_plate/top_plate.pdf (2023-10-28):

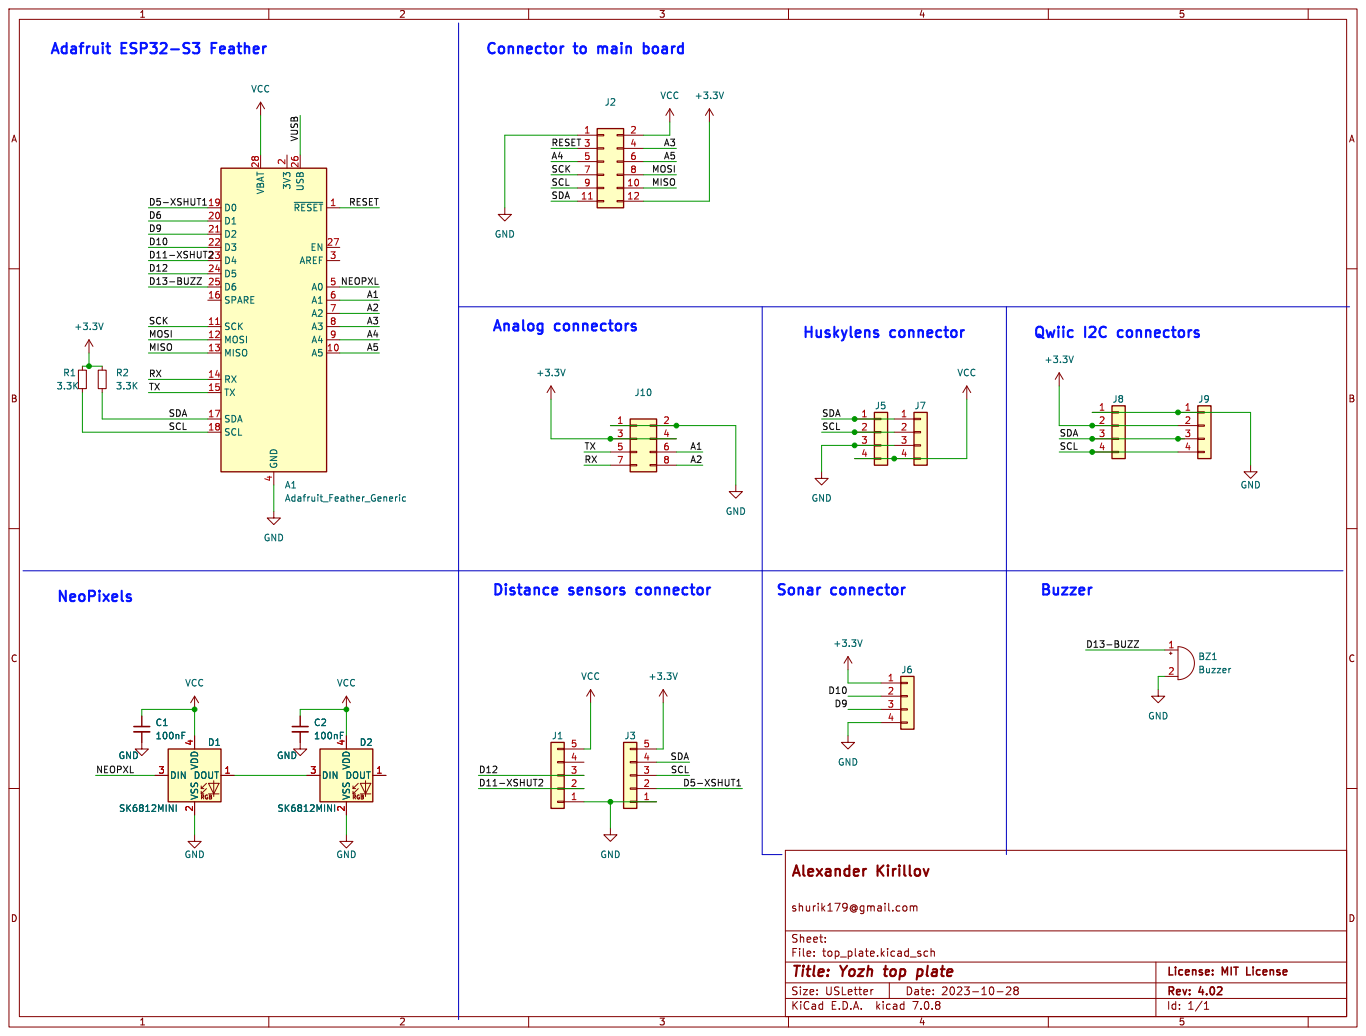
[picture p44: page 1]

Connector to main board

2 D1 20 D2 21 D3 22 D4 23 D5 24 D6 25 USB 26 EN 27 VBAT 28 AREF 3 GND

Id: 1/1 Title: Yozh top plate

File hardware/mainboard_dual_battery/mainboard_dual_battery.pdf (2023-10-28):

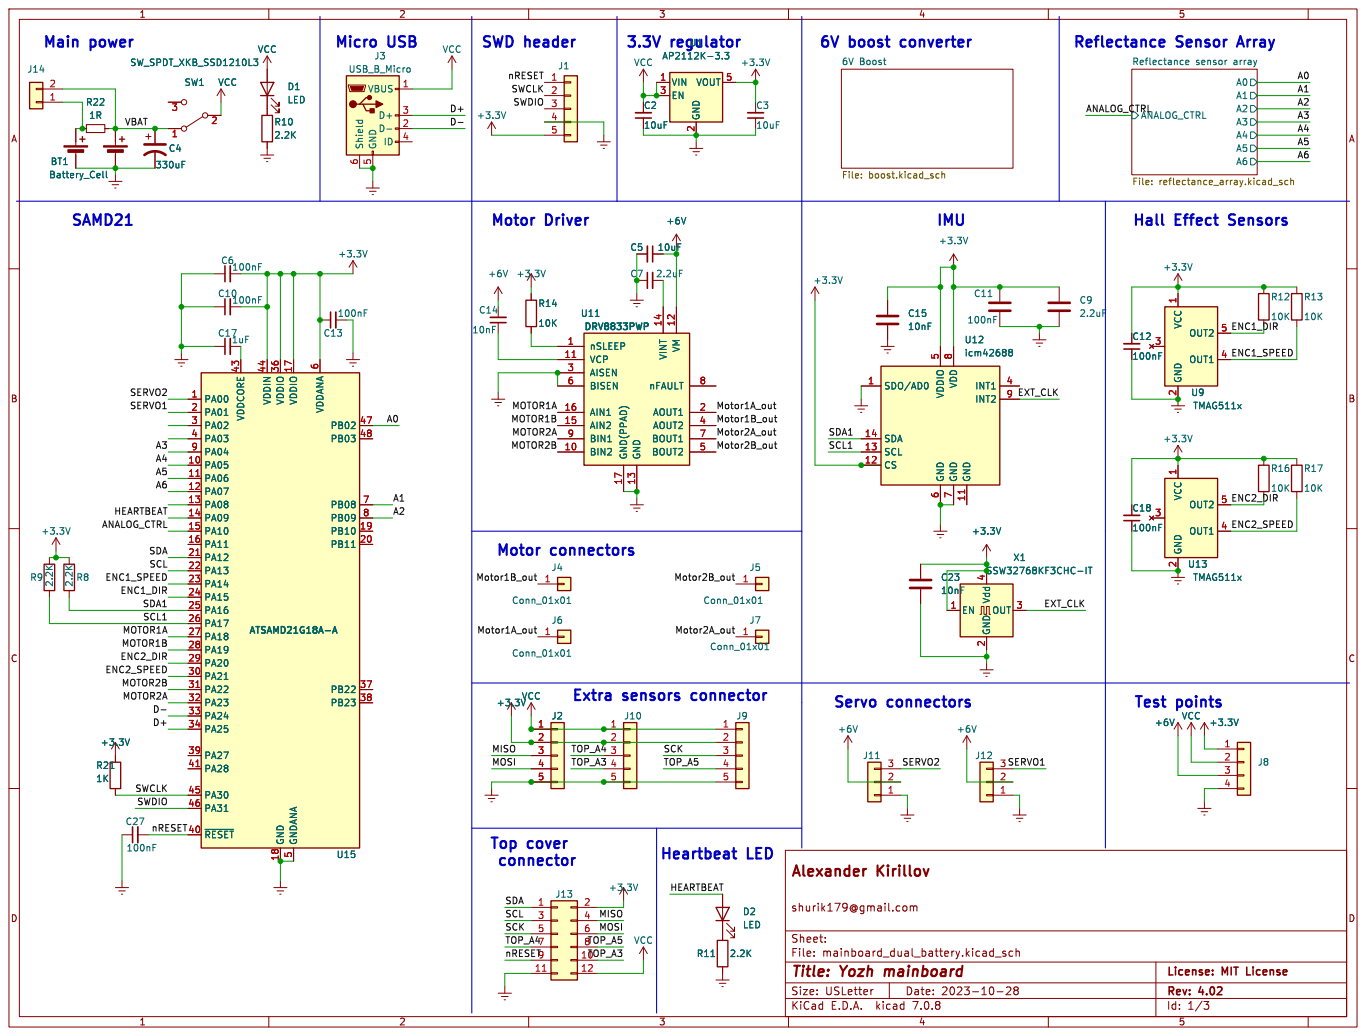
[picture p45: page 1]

Id: 1/3 Title: Yozh mainboard

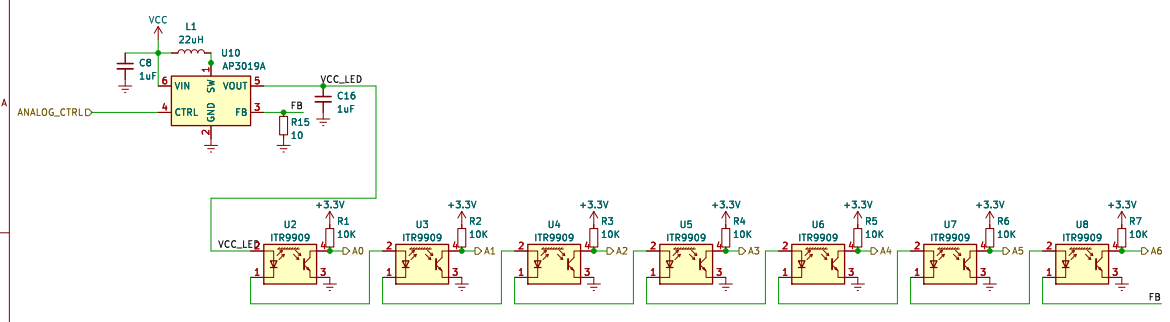
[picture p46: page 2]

2 FB 3 CTRL 4 VOUT 5 VIN 6 C8

Id: 2/3 Title: Yozh mainboard

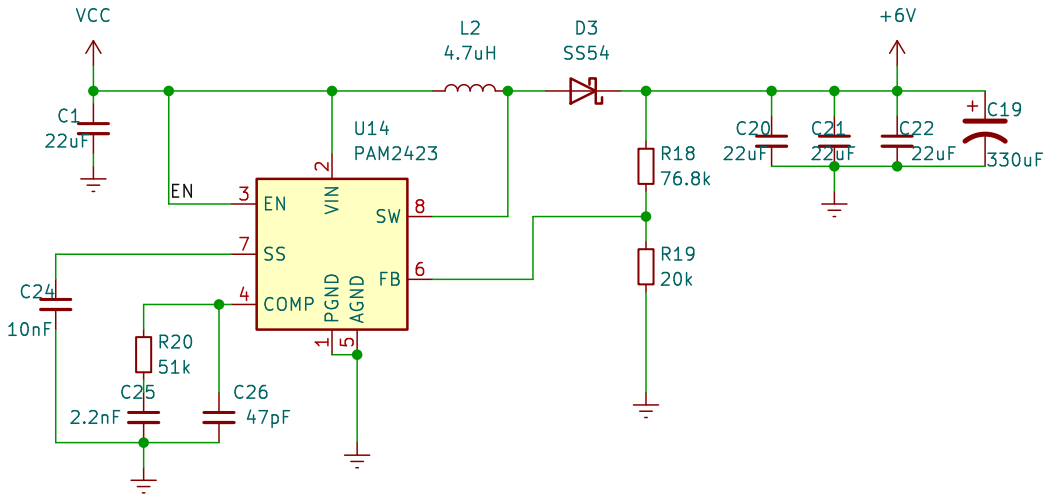
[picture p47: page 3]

Id: 3/3 Title: Yozh mainboard

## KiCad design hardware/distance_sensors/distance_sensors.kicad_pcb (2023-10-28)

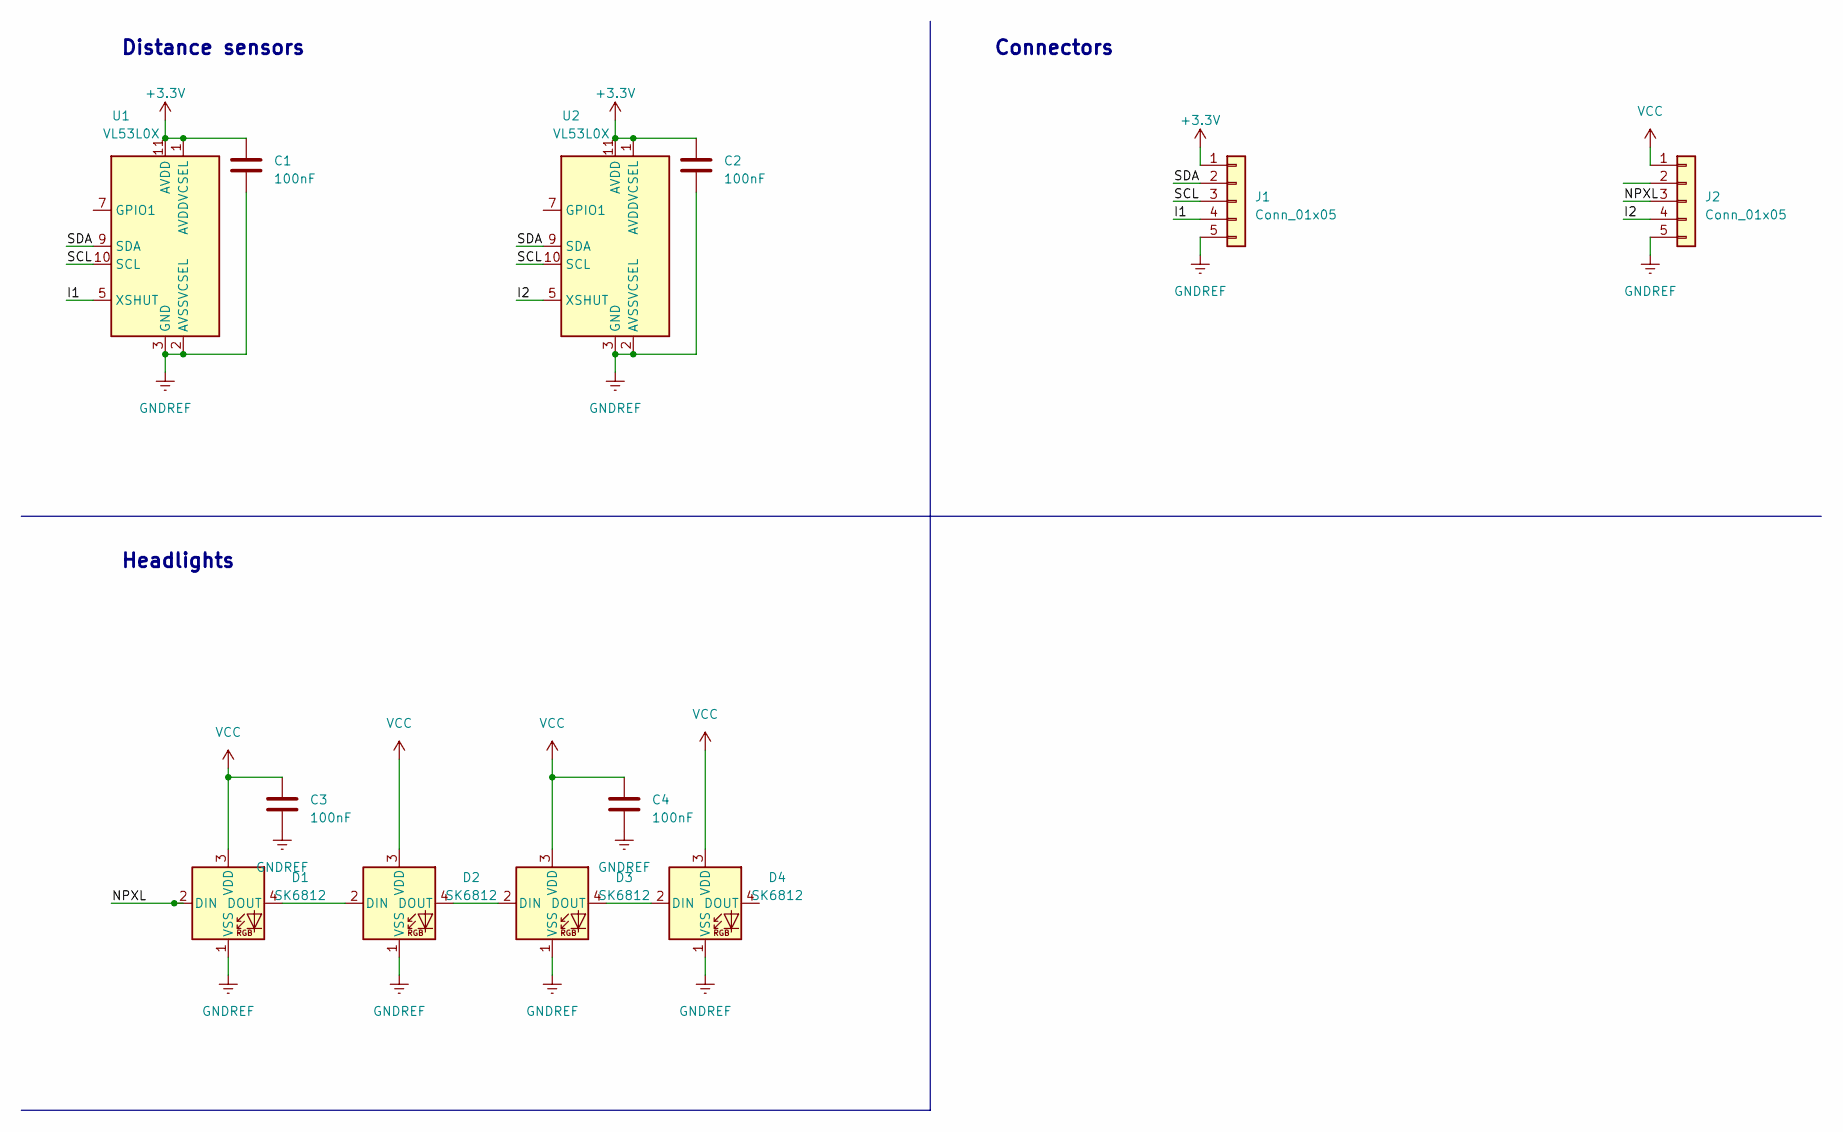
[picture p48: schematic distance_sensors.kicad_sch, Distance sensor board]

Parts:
C1, C2, C3, C4: 100nF; C_0603_1608Metric; LCSC C14663
D1, D2, D3, D4: SK6812; LED_SK6812_PLCC4_5.0x5.0mm_P3.2mm
J1, J2: Conn_01x05; PinSocket_1x05_P2.54mm_Vertical
U1, U2: VL53L0X; ST_VL53L1x; LCSC C91199

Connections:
+3V3: C1.1, C2.1, J1.1, U1.1 (AVDDVCSEL), U1.11 (AVDD), U2.1 (AVDDVCSEL), U2.11 (AVDD)
/I1: J1.4, U1.5 (XSHUT)
/I2: J2.4, U2.5 (XSHUT)
/NPXL: D1.2 (DIN), J2.3
/SCL: J1.3, U1.10 (SCL), U2.10 (SCL)
/SDA: J1.2, U1.9 (SDA), U2.9 (SDA)
GNDREF: C1.2, C2.2, C3.2, C4.2, D1.1 (VSS), D2.1 (VSS), D3.1 (VSS), D4.1 (VSS), J1.5, J2.5, U1.2 (AVSSVCSEL), U1.3 (GND), U1.4 (GND), U1.6 (GND), U1.12 (GND), U2.2 (AVSSVCSEL), U2.3 (GND), U2.4 (GND), U2.6 (GND), U2.12 (GND)
unnamed: D1.4 (DOUT), D2.2 (DIN)
unnamed: D2.4 (DOUT), D3.2 (DIN)
unnamed: D3.4 (DOUT), D4.2 (DIN)
VCC: C3.1, C4.1, D1.3 (VDD), D2.3 (VDD), D3.3 (VDD), D4.3 (VDD), J2.1

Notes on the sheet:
Distance sensors
Connectors
Headlights

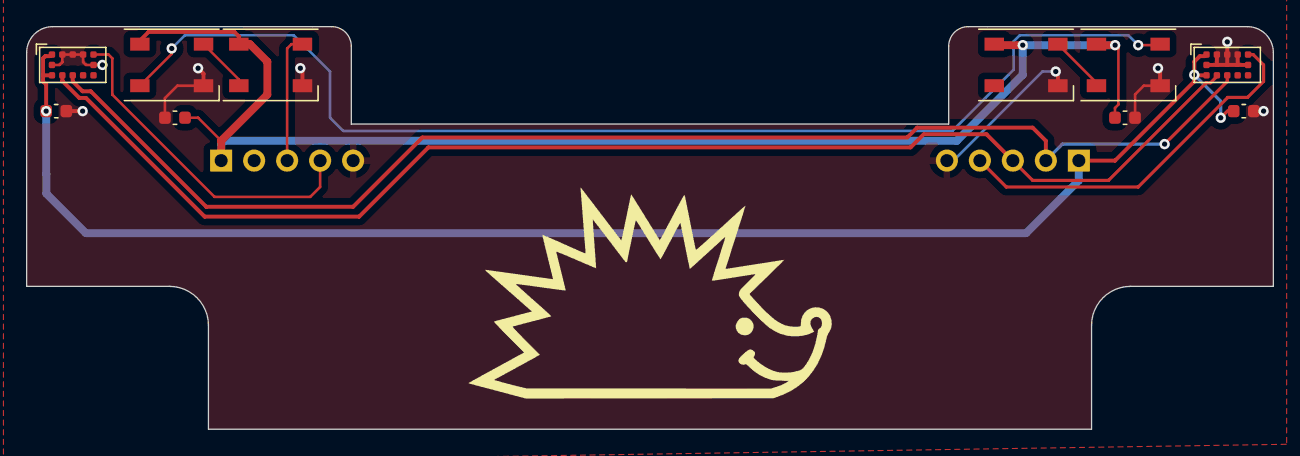
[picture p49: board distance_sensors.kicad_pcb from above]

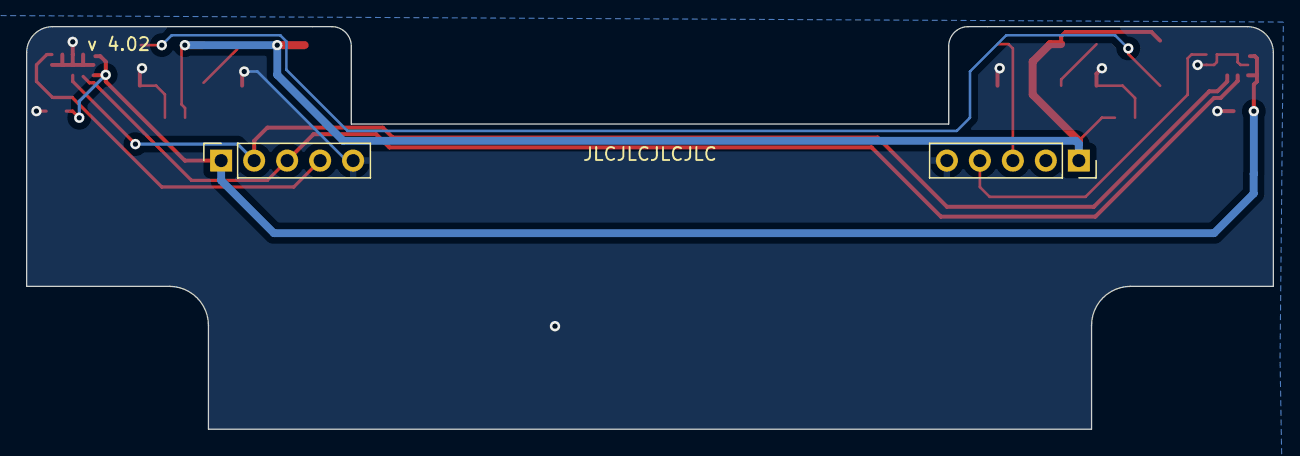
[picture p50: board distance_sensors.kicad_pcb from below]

Board: 2 copper layers, 96.0 x 31.0 mm, 12 parts (2 on the bottom side), 11 nets.

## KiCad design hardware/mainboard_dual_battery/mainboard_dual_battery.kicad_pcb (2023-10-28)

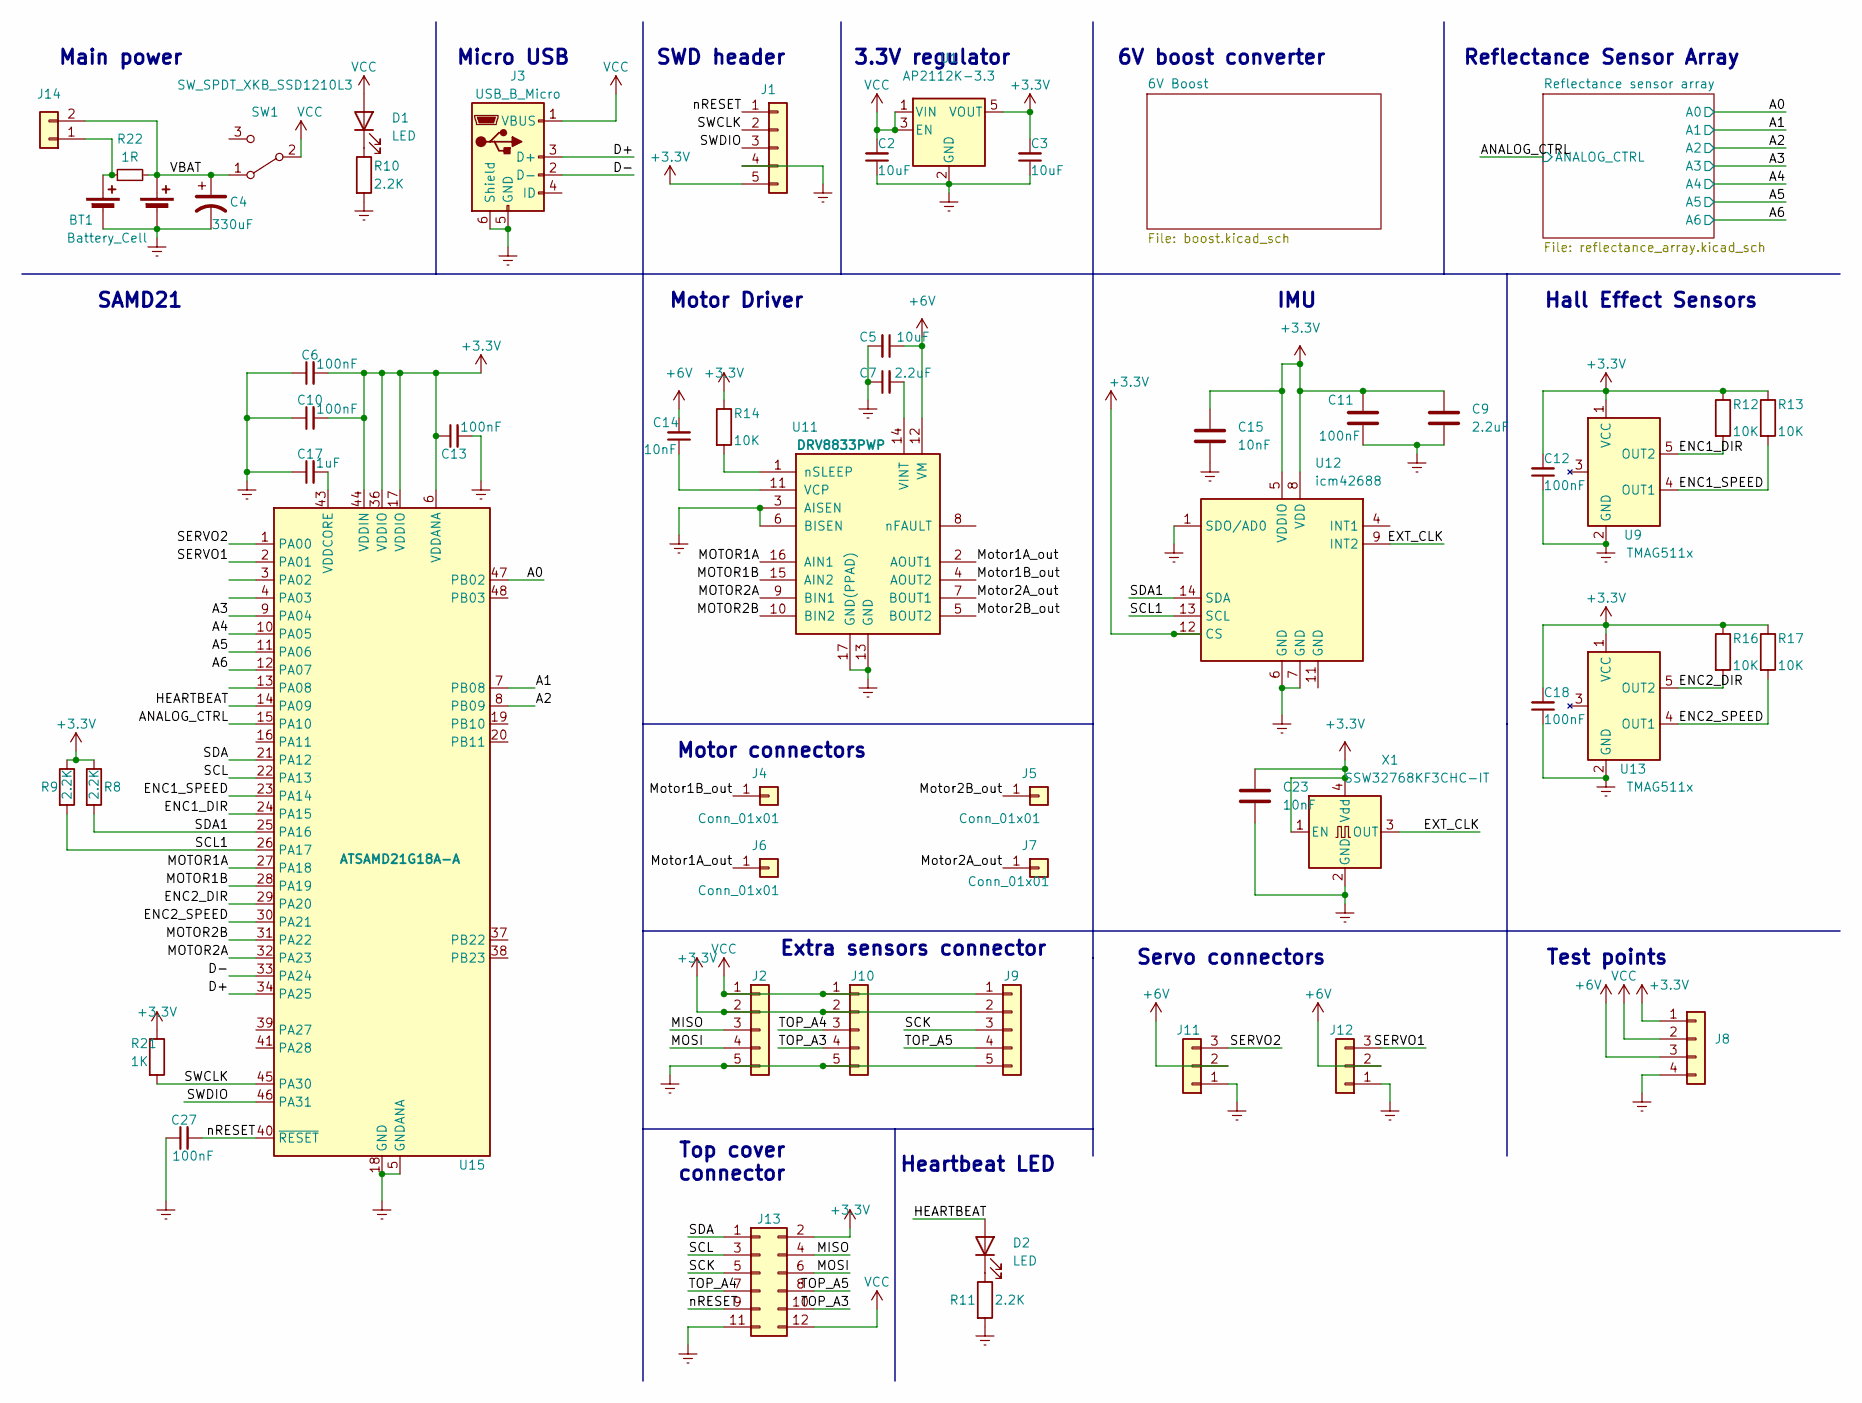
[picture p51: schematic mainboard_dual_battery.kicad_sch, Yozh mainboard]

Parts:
BT1: Battery_Cell; BatteryHolder_MYOUNG_BH-18650-B1BA007_2x18650; LCSC C6937126
C2, C3, C5: 10uF; C_0805_2012Metric; LCSC C15850
C4: 330uF; CP_Elec_6.3x7.7; LCSC C2980164
C6, C10, C11, C12, C13, C18, C27: 100nF; C_0603_1608Metric; LCSC C14663
C7, C9: 2.2uF; C_0603_1608Metric; LCSC C23630
C14, C15, C23: 10nF; C_0603_1608Metric; LCSC C57112
C17: 1uF; C_0603_1608Metric; LCSC C15849
D1, D2: LED; LED_0603_1608Metric; LCSC C72043
J1: Conn_01x05; PinSocket_1x05_P2.54mm_Lock
J2, J9, J10: Conn_01x05; PinHeader_1x05_P2.54mm_Vertical; LCSC C492404
J3: USB_B_Micro; USB_Micro-B_Amphenol_10118194_Horizontal; LCSC C132563
J4, J5, J6, J7: Conn_01x01; connector-1p-generic-nosilk
J8: Conn_01x04; connector-4p-generic-nosilk
J11, J12: Conn_01x03; PinHeader_1x03_P2.54mm_Vertical; LCSC C49257
J13: Conn_02x06_Odd_Even; PinSocket_2x06_P2.54mm_Vertical; LCSC C541855
J14: Conn_01x02; PinHeader_1x02_P2.54mm_Vertical
R8, R9, R10, R11: 2.2K; R_0603_1608Metric; LCSC C4190
R12, R13, R14, R16, R17: 10K; R_0603_1608Metric; LCSC C25804
R21: 1K; R_0603_1608Metric; LCSC C21190
R22: 1R; R_0603_1608Metric; LCSC C22936
SW1: SW_SPDT_XKB_SSD1210L3; SW_XKB_SS12D10L3; LCSC C319013
U1: AP2112K-3.3; SOT-23-5; LCSC C51118
U9, U13: TMAG511x; SOT-23-5
U11: DRV8833PWP; HTSSOP-16-1EP_4.4x5mm_P0.65mm_EP3.4x5mm_Mask2.46x2.31mm_The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; LCSC C50506
U12: icm42688; Bosch_LGA-14_3x2.5mm_P0.5mm; LCSC C1850418
U15: ATSAMD21G18A-A; QFP-48_7x7_Pitch0.5mm_reduced; LCSC C78624
X1: SSW32768KF3CHC-IT; Crystal_SMD_3225-4Pin_3.2x2.5mm_small_pads; LCSC C253931

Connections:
+3V3: C3.2, C6.2, C9.1, C10.2, C11.1, C12.2, C13.1, C15.1, C18.2, C23.1, J1.5, J2.2, J8.1, J9.2, J10.2, J13.2, R8.1, R9.1, R12.1, R13.1, R14.1, R16.1, R17.1, R21.1, U1.5 (VOUT), U9.1 (VCC), U12.5 (VDDIO), U12.8 (VDD), U12.12 (CS), U13.1 (VCC), U15.6 (VDDANA), U15.17 (VDDIO), U15.36 (VDDIO), U15.44 (VDDIN), X1.1 (EN), X1.4 (Vdd); also elsewhere on the board
/A0: U15.47 (PB02); also elsewhere on the board
/A1: U15.7 (PB08); also elsewhere on the board
/A2: U15.8 (PB09); also elsewhere on the board
/A3: U15.9 (PA04); also elsewhere on the board
/A4: U15.10 (PA05); also elsewhere on the board
/A5: U15.11 (PA06); also elsewhere on the board
/A6: U15.12 (PA07); also elsewhere on the board
/ANALOG_CTRL: U15.15 (PA10); also elsewhere on the board
/D+: J3.3 (D+), U15.34 (PA25)
/D-: J3.2 (D-), U15.33 (PA24)
/ENC1_DIR: R12.2, U9.5 (OUT2), U15.24 (PA15)
/ENC1_SPEED: R13.2, U9.4 (OUT1), U15.23 (PA14)
/ENC2_DIR: R16.2, U13.5 (OUT2), U15.29 (PA20)
/ENC2_SPEED: R17.2, U13.4 (OUT1), U15.30 (PA21)
/EXT_CLK: U12.9 (INT2), X1.3 (OUT)
/HEARTBEAT: D2.2 (A), U15.14 (PA09)
/MISO: J2.3, J13.4
/MOSI: J2.4, J13.6
/MOTOR1A: U11.16 (AIN1), U15.27 (PA18)
/MOTOR1B: U11.15 (AIN2), U15.28 (PA19)
/MOTOR2A: U11.9 (BIN1), U15.32 (PA23)
/MOTOR2B: U11.10 (BIN2), U15.31 (PA22)
/Motor1A_out: J6.1, U11.2 (AOUT1)
/Motor1B_out: J4.1, U11.4 (AOUT2)
/Motor2A_out: J7.1, U11.7 (BOUT1)
/Motor2B_out: J5.1, U11.5 (BOUT2)
/SCK: J9.3, J13.5
/SCL: J13.3, U15.22 (PA13)
/SCL1: R9.2, U12.13 (SCL), U15.26 (PA17)
/SDA: J13.1, U15.21 (PA12)
/SDA1: R8.2, U12.14 (SDA), U15.25 (PA16)
/SERVO1: J12.3, U15.2 (PA01)
/SERVO2: J11.3, U15.1 (PA00)
/SWCLK: J1.2, R21.2, U15.45 (PA30)
/SWDIO: J1.3, U15.46 (PA31)
/TOP_A3: J10.4, J13.10
/TOP_A4: J10.3, J13.7
/TOP_A5: J9.4, J13.8
/VBAT: BT1.3 (+), C4.1, J14.2, R22.2, SW1.1 (A)
/nRESET: C27.2, J1.1, J13.9, U15.40 (~RESET)
GNDREF: BT1.2 (-), BT1.4 (-), C2.1, C3.1, C4.2, C5.2, C6.1, C7.1, C9.2, C10.1, C11.2, C12.1, C13.2, C15.2, C17.1, C18.1, C23.2, C27.1, J1.4, J2.5, J3.5 (GND), J3.6 (Shield), J8.4, J9.5, J10.5, J11.1, J12.1, J13.11, R10.2, R11.2, U1.2 (GND), U9.2 (GND), U11.3 (AISEN), U11.6 (BISEN), U11.13 (GND), U11.17 (GND(PPAD)), U12.1 (SDO/AD0), U12.6 (GND), U12.7 (GND), U13.2 (GND), U15.5 (GNDANA), U15.18 (GND), U15.35 (GND), U15.42 (GND), X1.2 (GND); also elsewhere on the board
unnamed: D1.1 (K), R10.1
unnamed: D2.1 (K), R11.1
unnamed: BT1.1 (+), J14.1, R22.1
unnamed: C14.1, U11.11 (VCP)
unnamed: C7.2, U11.14 (VINT)
unnamed: R14.2, U11.1 (nSLEEP)
unnamed: C17.2, U15.43 (VDDCORE)

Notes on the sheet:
Hall Effect Sensors
IMU
6V boost converter
SWD header
3.3V regulator
Top cover connector
Servo connectors
Extra sensors connector
Motor Driver
SAMD21
Heartbeat LED
Main power
Motor connectors
Reflectance Sensor Array
Test points
Micro USB

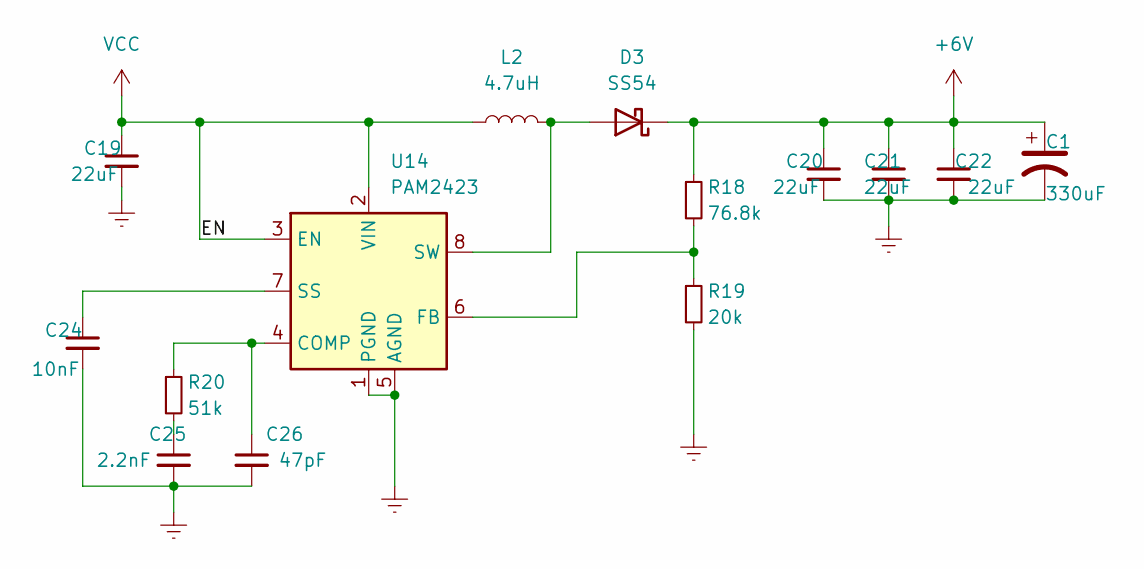
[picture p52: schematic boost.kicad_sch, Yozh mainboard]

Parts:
C1: 330uF; CP_Elec_6.3x7.7; LCSC C2980164
C19, C20, C21, C22: 22uF; C_0805_2012Metric; LCSC C45783
C24: 10nF; C_0603_1608Metric; LCSC C57112
C25: 2.2nF; C_0603_1608Metric; LCSC C1604
C26: 47pF; C_0603_1608Metric; LCSC C1671
D3: SS54; D_SMA; LCSC C22452
L2: 4.7uH; L_Panasonic-ETQP3M; LCSC C412309
R18: 76.8k; R_0603_1608Metric; LCSC C165743
R19: 20k; R_0603_1608Metric; LCSC C4184
R20: 51k; R_0603_1608Metric; LCSC C23196
U14: PAM2423; SOIC-8-1EP_3.9x4.9mm_P1.27mm_EP2.62x3.51mm; LCSC C781891

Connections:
GNDREF: C1.2, C19.2, C20.2, C21.2, C22.2, C24.2, C25.2, C26.2, R19.2, U14.1 (PGND), U14.5 (AGND); also elsewhere on the board
unnamed: C25.1, R20.2
unnamed: D3.2 (A), L2.2, U14.8 (SW)
unnamed: C26.1, R20.1, U14.4 (COMP)
unnamed: R18.2, R19.1, U14.6 (FB)
unnamed: C24.1, U14.7 (SS)

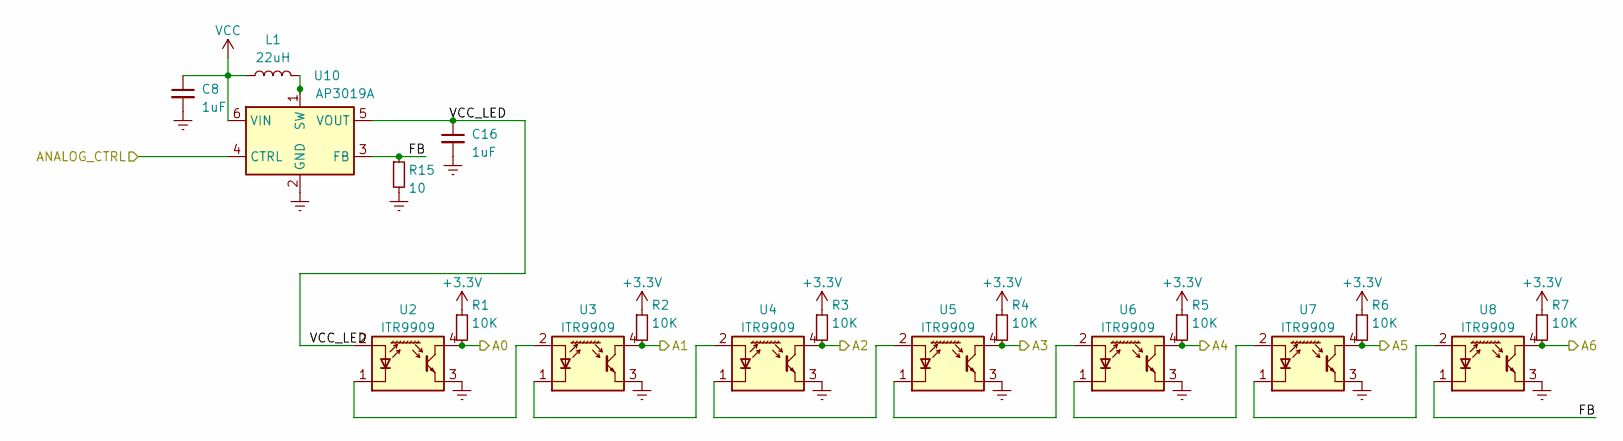
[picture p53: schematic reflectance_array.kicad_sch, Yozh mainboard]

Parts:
C8, C16: 1uF; C_0603_1608Metric; LCSC C15849
L1: 22uH; L_Taiyo-Yuden_NR-40xx; LCSC C2880384
R1, R2, R3, R4, R5, R6, R7: 10K; R_0603_1608Metric; LCSC C25804
R15: 10; R_0603_1608Metric; LCSC C319921
U2, U3, U4, U5, U6, U7, U8: ITR9909; Everlight_ITR9909; LCSC C53399
U10: AP3019A; TSOT-23-6; LCSC C44956

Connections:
+3V3: R1.1, R2.1, R3.1, R4.1, R5.1, R6.1, R7.1; also elsewhere on the board
/A0: R1.2, U2.4 (C); also elsewhere on the board
/A1: R2.2, U3.4 (C); also elsewhere on the board
/A2: R3.2, U4.4 (C); also elsewhere on the board
/A3: R4.2, U5.4 (C); also elsewhere on the board
/A4: R5.2, U6.4 (C); also elsewhere on the board
/A5: R6.2, U7.4 (C); also elsewhere on the board
/A6: R7.2, U8.4 (C); also elsewhere on the board
/ANALOG_CTRL: U10.4 (CTRL); also elsewhere on the board
/Reflectance sensor array/FB: R15.1, U8.1 (K), U10.3 (FB)
/Reflectance sensor array/VCC_LED: C16.1, U2.2 (A), U10.5 (VOUT)
GNDREF: C8.2, C16.2, R15.2, U2.3 (E), U3.3 (E), U4.3 (E), U5.3 (E), U6.3 (E), U7.3 (E), U8.3 (E), U10.2 (GND); also elsewhere on the board
unnamed: U2.1 (K), U3.2 (A)
unnamed: U3.1 (K), U4.2 (A)
unnamed: U4.1 (K), U5.2 (A)
unnamed: U5.1 (K), U6.2 (A)
unnamed: U6.1 (K), U7.2 (A)
unnamed: U7.1 (K), U8.2 (A)
unnamed: L1.2, U10.1 (SW)

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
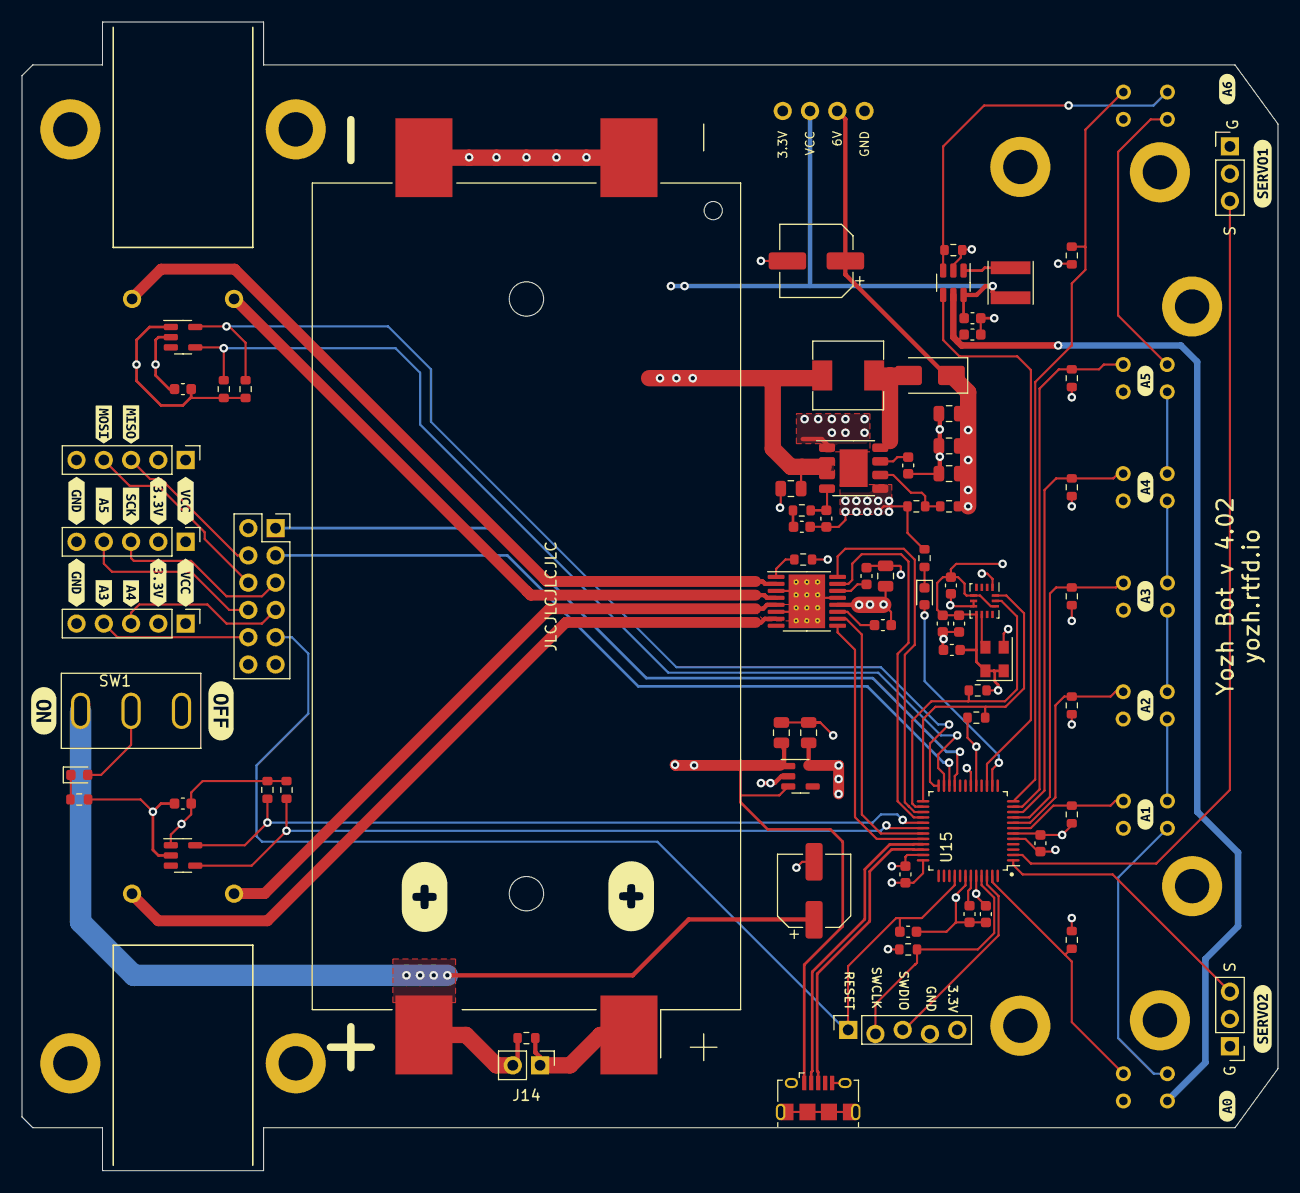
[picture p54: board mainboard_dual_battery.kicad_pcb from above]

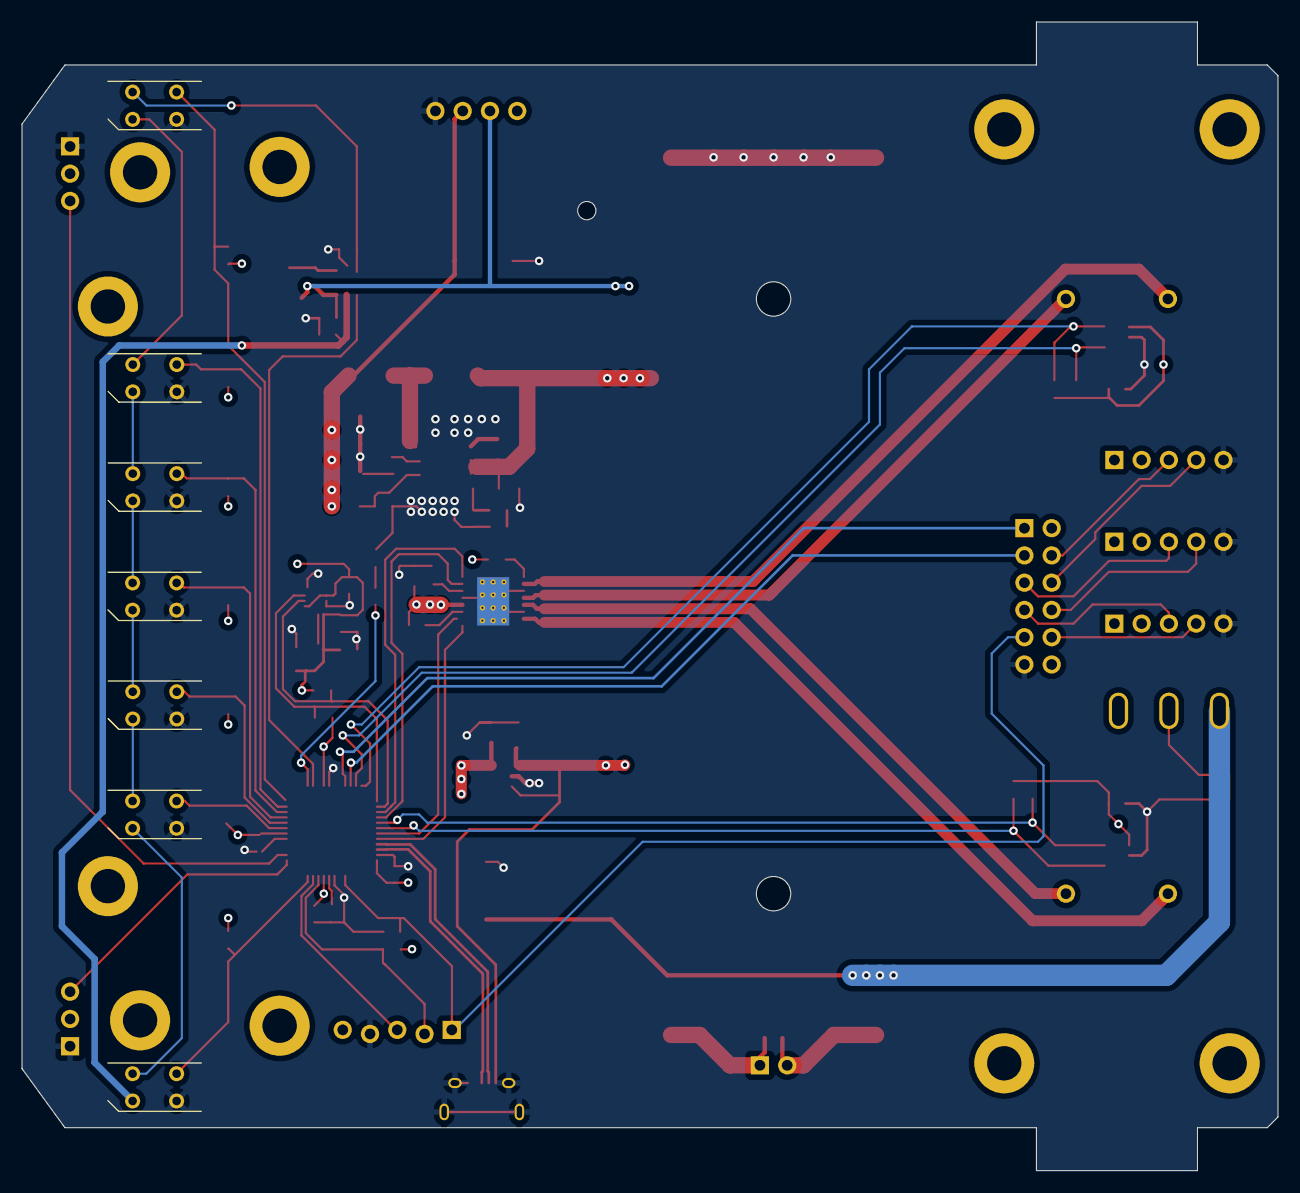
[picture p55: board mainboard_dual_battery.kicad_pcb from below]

Board: 4 copper layers, 117.0 x 107.0 mm, 111 parts (7 on the bottom side), 65 nets.

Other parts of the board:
kibuzzard-653BD0CB: G***; kibuzzard-653BD0CB
kibuzzard-653BD1D9: G***; kibuzzard-653BD1D9
kibuzzard-653BD1F8: G***; kibuzzard-653BD1F8
kibuzzard-653BD3E9, kibuzzard-653BD3E9#2: G***; kibuzzard-653BD3E9
kibuzzard-653BD5EB: G***; kibuzzard-653BD5EB
kibuzzard-653BD15F: G***; kibuzzard-653BD15F
kibuzzard-653BD22E: G***; kibuzzard-653BD22E
kibuzzard-653BD101: G***; kibuzzard-653BD101
kibuzzard-653BD134: G***; kibuzzard-653BD134
kibuzzard-653BD153: G***; kibuzzard-653BD153
kibuzzard-653BD166: G***; kibuzzard-653BD166
kibuzzard-653BD170: G***; kibuzzard-653BD170
kibuzzard-653BD252: G***; kibuzzard-653BD252
kibuzzard-653BD666: G***; kibuzzard-653BD666
kibuzzard-653BDAE1: G***; kibuzzard-653BDAE1
kibuzzard-653BDB0C: G***; kibuzzard-653BDB0C
kibuzzard-653BDB2A: G***; kibuzzard-653BDB2A
kibuzzard-653BDB3F: G***; kibuzzard-653BDB3F
kibuzzard-653BDB4D: G***; kibuzzard-653BDB4D
kibuzzard-653BDB7B: G***; kibuzzard-653BDB7B
kibuzzard-653BDB20: G***; kibuzzard-653BDB20
kibuzzard-653BDB31: G***; kibuzzard-653BDB31
kibuzzard-653BDB46: G***; kibuzzard-653BDB46
kibuzzard-653BDB91: G***; kibuzzard-653BDB91

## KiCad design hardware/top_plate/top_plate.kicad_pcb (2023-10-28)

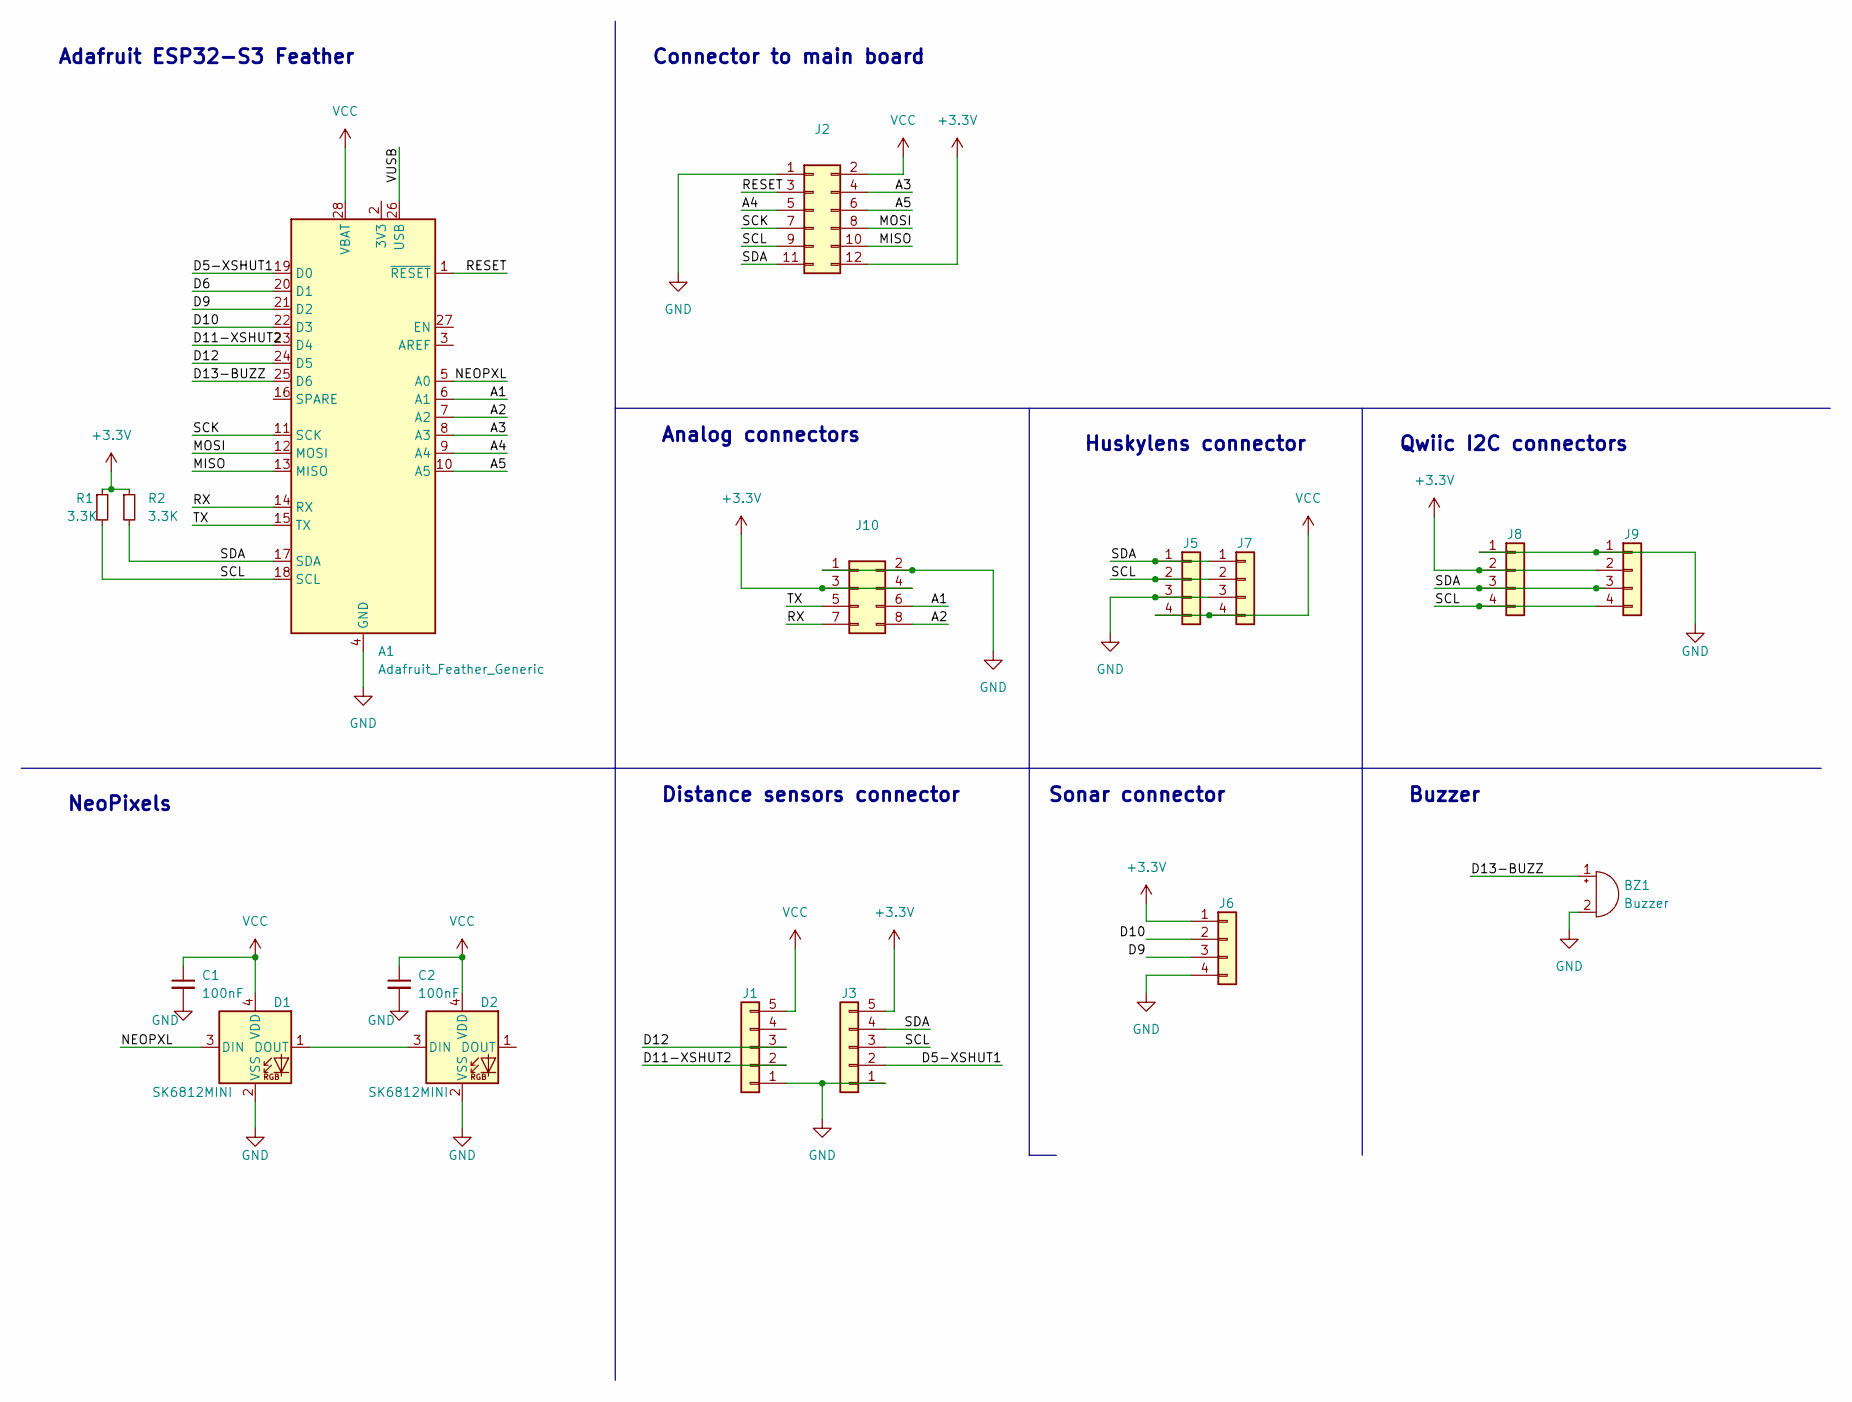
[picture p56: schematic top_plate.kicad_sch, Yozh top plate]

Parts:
A1: Adafruit_Feather_Generic; Adafruit_Feather
BZ1: Buzzer; Buzzer_TDK_PS1240P02BT_D12.2mm_H6.5mm
C1, C2: 100nF; C_0603_1608Metric; LCSC C14663
D1, D2: SK6812MINI; LED_SK6812MINI_PLCC4_3.5x3.5mm_P1.75mm; LCSC C2886570
J1, J3: Conn_01x05; PinHeader_1x05_P2.54mm_Horizontal
J2: Conn_02x06_Odd_Even; PinSocket_2x06_P2.54mm_Vertical
J5: Conn_01x04; JST_PH_B4B-PH-K_1x04_P2.00mm_Vertical; LCSC C131334
J6: Conn_01x04; connector-4p-generic-nosilk
J7: Conn_01x04; connector-4p-generic-nosilk; LCSC C2691448
J8, J9: Conn_01x04; JST_SH_BM04B-SRSS-TB_1x04-1MP_P1.00mm_Vertical; LCSC C160390
J10: Conn_02x04_Odd_Even; PinHeader_2x04_P2.54mm_Vertical
R1, R2: 3.3K; R_0603_1608Metric; LCSC C22978

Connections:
+3V3: J2.12, J3.5, J6.1, J8.2, J9.2, J10.3, J10.4, R1.1, R2.1
/A1: A1.6 (A1), J10.6
/A2: A1.7 (A2), J10.8
/A3: A1.8 (A3), J2.4
/A4: A1.9 (A4), J2.5
/A5: A1.10 (A5), J2.6
/D5-XSHUT1: A1.19 (D0), J3.2
/D6: A1.20 (D1)
/D9: A1.21 (D2), J6.3
/D10: A1.22 (D3), J6.2
/D11-XSHUT2: A1.23 (D4), J1.2
/D12: A1.24 (D5), J1.3
/D13-BUZZ: A1.25 (D6), BZ1.1 (-)
/MISO: A1.13 (MISO), J2.10
/MOSI: A1.12 (MOSI), J2.8
/NEOPXL: A1.5 (A0), D1.3 (DIN)
/RESET: A1.1 (~RESET), J2.3
/RX: A1.14 (RX), J10.7
/SCK: A1.11 (SCK), J2.7
/SCL: A1.18 (SCL), J2.9, J3.3, J5.2, J7.2, J8.4, J9.4, R1.2
/SDA: A1.17 (SDA), J2.11, J3.4, J5.1, J7.1, J8.3, J9.3, R2.2
/TX: A1.15 (TX), J10.5
/VUSB: A1.26 (USB)
GND: A1.4 (GND), BZ1.2 (+), C1.2, C2.2, D1.2 (VSS), D2.2 (VSS), J1.1, J2.1, J3.1, J5.3, J6.4, J7.3, J8.1, J9.1, J10.1, J10.2
unnamed: D1.1 (DOUT), D2.3 (DIN)
VCC: A1.28 (VBAT), C1.1, C2.1, D1.4 (VDD), D2.4 (VDD), J1.5, J2.2, J5.4, J7.4

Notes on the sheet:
Analog connectors
Buzzer
Adafruit ESP32-S3 Feather
Distance sensors connector
NeoPixels
Sonar connector
Huskylens connector
Connector to main board
Qwiic I2C connectors

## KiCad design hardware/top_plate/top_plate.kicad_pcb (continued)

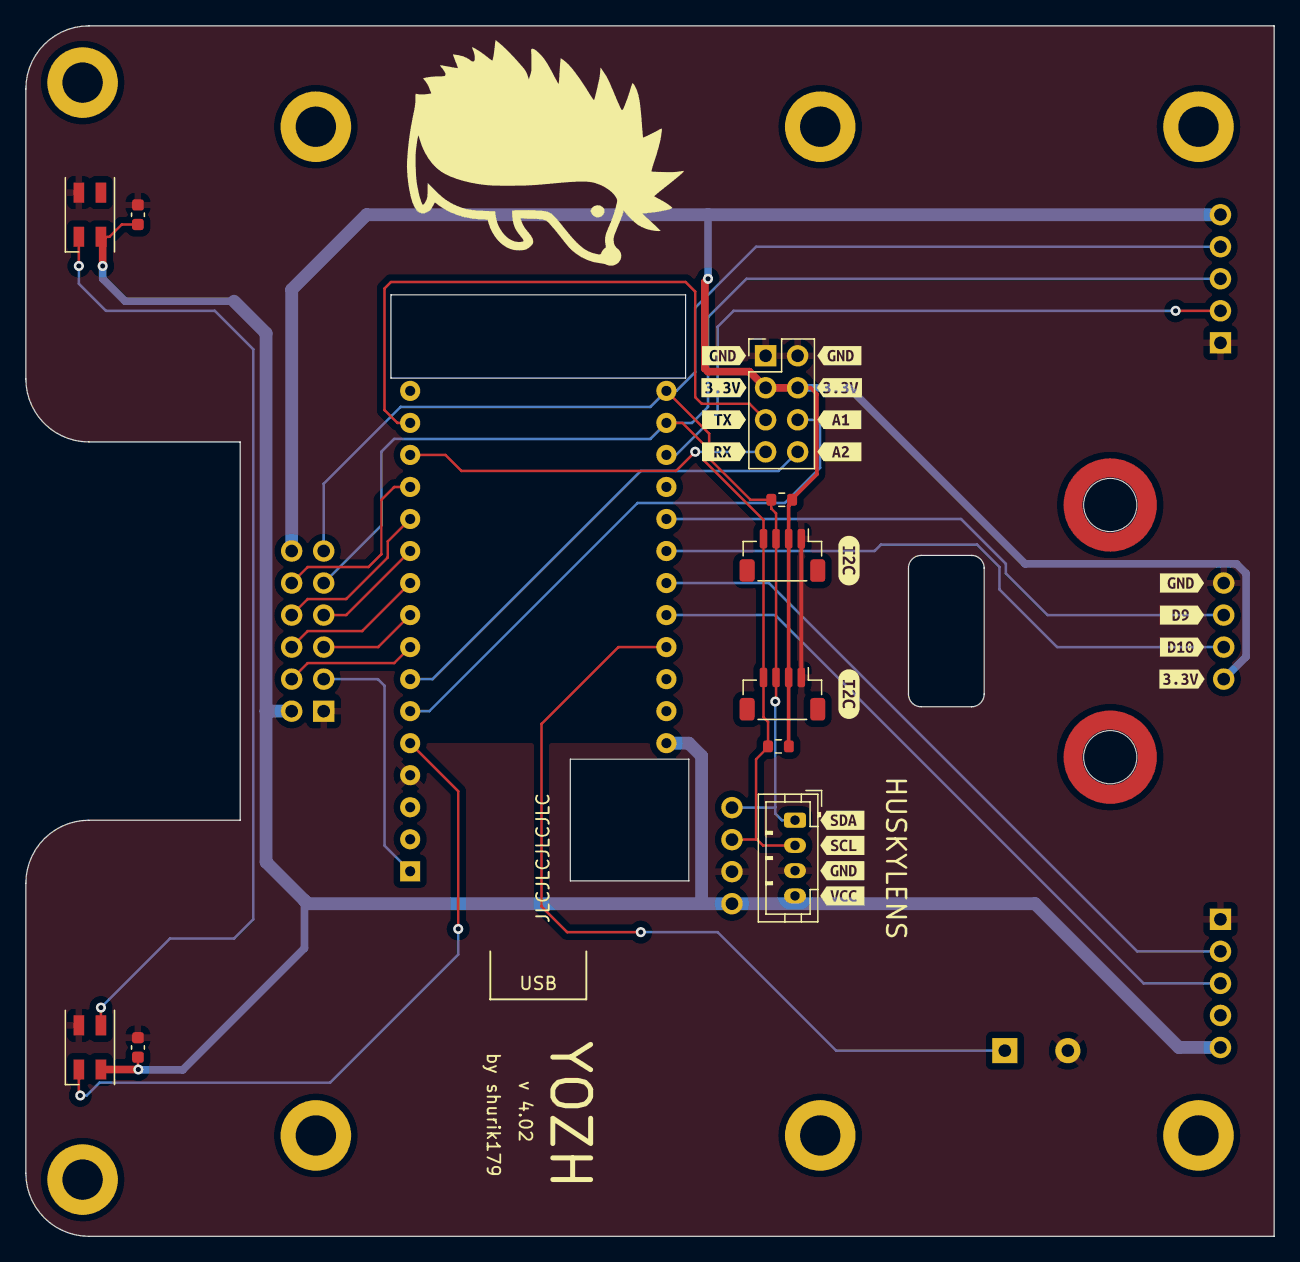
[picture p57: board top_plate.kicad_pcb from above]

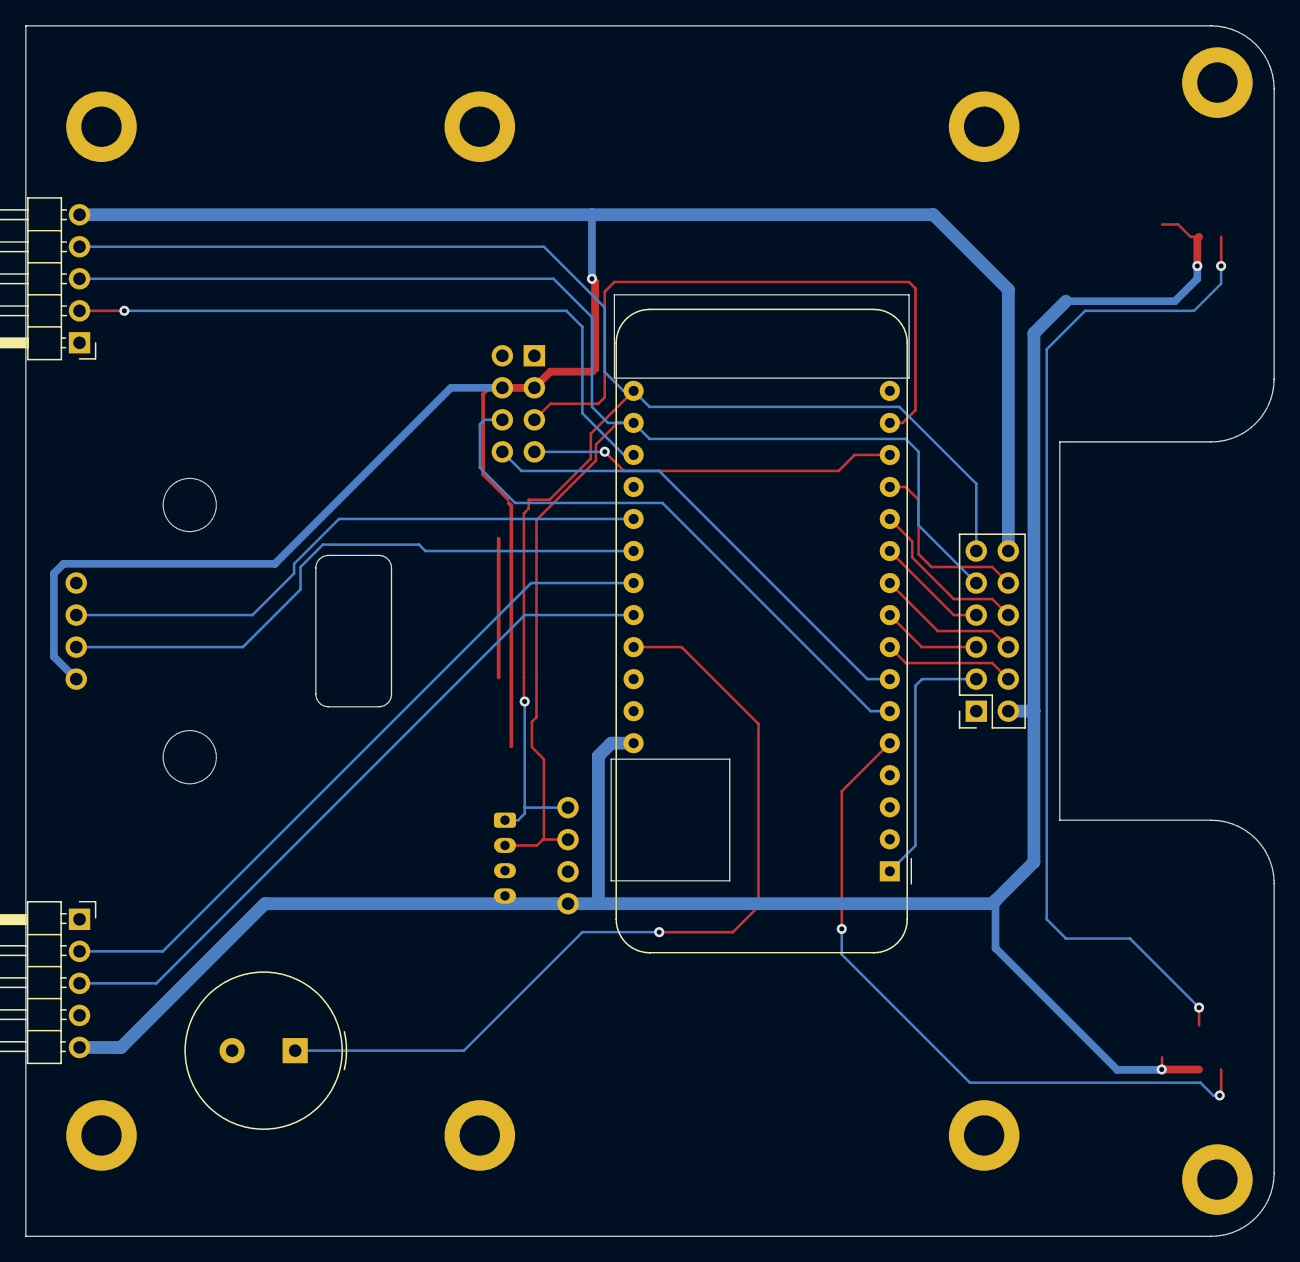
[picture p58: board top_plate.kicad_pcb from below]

Board: 2 copper layers, 99.0 x 96.0 mm, 37 parts (5 on the bottom side), 24 nets.

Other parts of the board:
M1, M2: SMTSO3035; mounting_SMD_NUT_M3_H6mm
kibuzzard-653BCB65, kibuzzard-653BCB65#2: G***; kibuzzard-653BCB65
kibuzzard-653BCCF1, kibuzzard-653BCCF1#2: G***; kibuzzard-653BCCF1
kibuzzard-653BCD2B: G***; kibuzzard-653BCD2B
kibuzzard-653BCD4B: G***; kibuzzard-653BCD4B
kibuzzard-653BCD42: G***; kibuzzard-653BCD42
kibuzzard-653BCDC1, kibuzzard-653BCDC1#2: G***; kibuzzard-653BCDC1
kibuzzard-653BCDD4: G***; kibuzzard-653BCDD4
kibuzzard-653BCDDF: G***; kibuzzard-653BCDDF
kibuzzard-653BCDE7: G***; kibuzzard-653BCDE7
kibuzzard-653BCECF: G***; kibuzzard-653BCECF
kibuzzard-653BCED5: G***; kibuzzard-653BCED5
kibuzzard-653BCEE0: G***; kibuzzard-653BCEE0
kibuzzard-653BCF3B: G***; kibuzzard-653BCF3B
kibuzzard-653BCF4B: G***; kibuzzard-653BCF4B
kibuzzard-653BCF42: G***; kibuzzard-653BCF42

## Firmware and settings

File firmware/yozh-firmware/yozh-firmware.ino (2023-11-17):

// SPDX-FileCopyrightText: Copyright 2021-2023 Alexander Kirillov <shurik179@gmail.com>
// SPDX-License-Identifier: MIT

//#include "wiring_private.h"
//registers
#include "regmap.h"
#include "i2c.h"
//code for motors, encoders, and servos
#include "motors.h"
#include "analog.h"
#include "IMU.h"

#define FW_VERSION_MAJOR 4
#define FW_VERSION_MINOR 02

//uncomment to allow debugging print to Serial.
//#define DEBUG_PRINT

uint32_t loopCount=0;
uint32_t lastBlink=0;
bool heartbeat = 0;

void setup(){
    i2cMasterBegin(100000); //start I2C bus on Wire1 as master, in regular mode (100 kHz)
    i2cSlaveBegin();        //start i2c bus on Wire, as a slave
    initRegmap();
    *whoAmI=0x11;
    fwVersion[0]=FW_VERSION_MINOR;
    fwVersion[1]=FW_VERSION_MAJOR;
#ifdef DEBUG_PRINT
        Serial.begin(9600);
        /*while(!Serial){
          delay(10);
        }*/
        delay(2000);
        Serial.println("Yozh firmware started");
        delay(1000);
#endif
    for (int i=0; i<2; i++){
        servoPosition[i] = 0;
    }
    *motorMode = MOTOR_MODE_POWER;
    setupTimers();
    setupMotorPins();
    setServos();//FIXME
    *linearrayConfig = 0;
    pinMode(PIN_HEARTBEAT, OUTPUT);
    digitalWrite(PIN_HEARTBEAT, LOW);
    * imuConfig = 1;
    IMUbegin();
    Serial.println("Setup ends");
}

void loop(){
    loopCount++;
    //blink LED
    uint32_t now = millis();
    if (now-lastBlink>250) {
        lastBlink = now;
        heartbeat = ! heartbeat;
        digitalWrite(PIN_HEARTBEAT, heartbeat);
    }
    //First, update configuration/motors/servos
    if (isSet(FLAG_MOTOR_CONFIG)){
        clearFlag(FLAG_MOTOR_CONFIG);
        #ifdef DEBUG_PRINT
            Serial.println("Updating motor configuration");
        #endif
        //FIXME - need to restart all PID controllers
    }
    if (isSet(FLAG_SERVO)){
        clearFlag(FLAG_SERVO);//unset the servo flag bit
        #ifdef DEBUG_PRINT
        Serial.print("setting servo to new positions: ");
        Serial.print(servoPosition[0]); Serial.println(" ");
        Serial.print(servoPosition[1]); Serial.println(" ");
        #endif
        setServos();
    }
    if (isSet(FLAG_ENC_RESET)) {
        clearFlag(FLAG_ENC_RESET);
        #ifdef DEBUG_PRINT
        Serial.println("Resetting encoder(s)");
        #endif
        resetEncoders();
    }
    if (isSet(FLAG_MOTOR_MODE)||isSet(FLAG_MOTOR_POWER)){
        clearFlag(FLAG_MOTOR_MODE);
        clearFlag(FLAG_MOTOR_POWER);
        #ifdef DEBUG_PRINT
            Serial.println("Updating motor mode/power  configuration");
            Serial.print("Motor mode: "); Serial.print(*motorMode);
            Serial.print(" powerL: "); Serial.print(motorPower[0]);
            Serial.print(" powerR: "); Serial.println(motorPower[1]);
        #endif
        setMotors();
    }
    if (isSet(FLAG_LINEARRAY_CONFIG)){
        clearFlag(FLAG_LINEARRAY_CONFIG);
        if (*linearrayConfig) {
            enableLineArray();
        } else {
            disableLineArray();
        }
    }

    if (isSet(FLAG_IMU_CONFIG)){
        clearFlag(FLAG_IMU_CONFIG);
        #ifdef DEBUG_PRINT
        Serial.println("Configuring IMU");
        #endif
        switch (*imuConfig){
            case IMU_CONFIG_END: //stop
                *imuStatus = IMU_OFF;
                break;
            case IMU_CONFIG_BEGIN://begin
                *imuStatus = IMU_OK; //FIXME
                //Serial.println("starting IMU");
                IMUbegin();
                //Serial.println("IMU Started");
                break;
            case IMU_CONFIG_CALIBRATE: //calibrate
                IMUcalibrate();
                break;
        }
    }

    //now, update readings of sensors etc
    if (*imuConfig) {
        IMUupdate();
    }
    if (*linearrayConfig) {
        updateLineArray();
    }

    //update motor speed reading and pid speed adjustment
    //it will automatically check for elapsed  time
    updateSpeed();

}

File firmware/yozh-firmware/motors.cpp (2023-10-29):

// SPDX-FileCopyrightText: Copyright 2021-2023 Alexander Kirillov <shurik179@gmail.com>
// SPDX-License-Identifier: MIT
#include "motors.h"
#include "pid.h"
#include "regmap.h"

//
int32_t volatile encoderTimestamp[]={0,0};     // time of last encoder update, in micros
int32_t prevEncoder[]={0,0};          // to hold previous values of encoders - for computing speed
int32_t prevEncoderTimestamp[]={0,0}; // time of previous encoder update, in micros
//volatile int8_t   motorDirection[]={1,1}; // motor directions: +1 for forward, -1 for backwards
uint32_t lastUpdate = 0;

//motor speed controllers
PIDcontroller CourseController;

void setupTimers () {
    //setup the clock
    REG_GCLK_GENDIV = GCLK_GENDIV_DIV(3) |          // Divide the 48MHz clock source by divisor 3: 48MHz/3=16MHz
                    GCLK_GENDIV_ID(4);            // Select Generic Clock (GCLK) 4
    while (GCLK->STATUS.bit.SYNCBUSY);              // Wait for synchronization

    REG_GCLK_GENCTRL = GCLK_GENCTRL_IDC |           // Set the duty cycle to 50/50 HIGH/LOW
                   GCLK_GENCTRL_GENEN |           // Enable GCLK4
                   GCLK_GENCTRL_SRC_DFLL48M |     // Set the 48MHz clock source
                   GCLK_GENCTRL_ID(4);            // Select GCLK4
    while (GCLK->STATUS.bit.SYNCBUSY);              // Wait for synchronization
    //feed GCLK4 to TCC0, TCC1
    REG_GCLK_CLKCTRL = GCLK_CLKCTRL_CLKEN |          // Enable GCLK
                       GCLK_CLKCTRL_GEN_GCLK4 |    // Select GCLK4
                       GCLK_CLKCTRL_ID_TCC0_TCC1;  // Feed GCLK4 to TCC0 and TCC1
    while (GCLK->STATUS.bit.SYNCBUSY);               // Wait for synchronization

    REG_GCLK_CLKCTRL = GCLK_CLKCTRL_CLKEN |          // Enable GCLK
                       GCLK_CLKCTRL_GEN_GCLK4 |    // Select GCLK4
                       GCLK_CLKCTRL_ID_TCC2_TC3;   // Feed GCLK4 to TCC2 and TC3
    while (GCLK->STATUS.bit.SYNCBUSY);               // Wait for synchronization

    //configure TCC0 timer for motors
    // Normal (single slope) PWM operation: timers countinuously count up to PER register value and then is reset to 0
    REG_TCC0_WAVE |= TCC_WAVE_WAVEGEN_NPWM;        // Setup single slope PWM on TCC0
    while (TCC0->SYNCBUSY.bit.WAVE);               // Wait for synchronization
    REG_TCC0_PER = 500;                            // period = 501 ticks, so freq is  16Mhz/501 approx 32 Khz
    while(TCC0->SYNCBUSY.bit.PER);
    // Set prescaler and enable the outputs
    REG_TCC0_CTRLA |= TCC_CTRLA_PRESCALER_DIV1 |    // Divide GCLK4 by 1
                        TCC_CTRLA_ENABLE;         // Enable the TCC0 output
    while (TCC0->SYNCBUSY.bit.ENABLE);              // Wait for synchronization

    //configure TCC1 timer for servos
    // Normal (single slope) PWM operation: timers countinuously count up to PER register value and then is reset to 0
    /* REG_TCC1_WAVE |= TCC_WAVE_WAVEGEN_NPWM;        // Setup single slope PWM on TCC1
    while (TCC1->SYNCBUSY.bit.WAVE);               // Wait for synchronization
    REG_TCC1_PER = 19999;                          // period = 20 000 us, so freq is  50 hz
    while(TCC1->SYNCBUSY.bit.PER);*/
    //configure TCC2 timer for servos
    // Normal (single slope) PWM operation: timers countinuously count up to PER register value and then is reset to 0
    REG_TCC2_WAVE |= TCC_WAVE_WAVEGEN_NPWM;        // Setup single slope PWM on TCC2
    while (TCC2->SYNCBUSY.bit.WAVE);               // Wait for synchronization
    REG_TCC2_PER = 19999;                          // period = 20 000 us, so freq is  50 hz
    while(TCC2->SYNCBUSY.bit.PER);


    /*
      // Set prescaler and enable the outputs
      REG_TCC1_CTRLA |= TCC_CTRLA_PRESCALER_DIV16 |    // Divide GCLK4 by 16
                            TCC_CTRLA_ENABLE;          // Enable the TCC1 output
      while (TCC1->SYNCBUSY.bit.ENABLE);               // Wait for synchronization
    */
    // Set prescaler and enable the outputs
    REG_TCC2_CTRLA |= TCC_CTRLA_PRESCALER_DIV16 |    // Divide GCLK4 by 16
                        TCC_CTRLA_ENABLE;          // Enable the TCC2 output
    while (TCC2->SYNCBUSY.bit.ENABLE);               // Wait for synchronization
}
void setupMotorPins(){
    pinPeripheral(PIN_SERVO1, PIO_TIMER);
    pinPeripheral(PIN_SERVO2, PIO_TIMER);
    pinPeripheral(PIN_MOTOR1A, PIO_TIMER_ALT);
    pinPeripheral(PIN_MOTOR1B, PIO_TIMER_ALT);
    pinPeripheral(PIN_MOTOR2A, PIO_TIMER_ALT);
    pinPeripheral(PIN_MOTOR2B, PIO_TIMER_ALT);
    pinMode(PIN_ENC1_DIR, INPUT);
    pinMode(PIN_ENC2_DIR, INPUT);
    //attachInterrupt(digitalPinToInterrupt(PIN_ENC1_DIR), ISR_enc1_dir, CHANGE);
    attachInterrupt(digitalPinToInterrupt(PIN_ENC1_SPEED), ISR_enc1_speed, CHANGE);
    //attachInterrupt(digitalPinToInterrupt(PIN_ENC2_DIR), ISR_enc2_dir, CHANGE);
    attachInterrupt(digitalPinToInterrupt(PIN_ENC2_SPEED), ISR_enc2_speed, CHANGE);
}

void resetEncoders(){
    //using encoder variable, defined at regmap.cpp
    encoder[0]=0;
    encoder[1]=0;
    //also, reset previous value, otherwise speed computation will go haywire
    prevEncoder[0]=0;
    prevEncoder[1]=0;
    lastUpdate = micros();
}
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

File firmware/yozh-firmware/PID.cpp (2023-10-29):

// SPDX-FileCopyrightText: Copyright 2021-2023 Alexander Kirillov <shurik179@gmail.com>
// SPDX-License-Identifier: MIT
#include "PID.h"

void PIDcontroller::configure(volatile  float p, volatile  float i, volatile  float d){
  Kp=p;
  Ki=i;
  Kd=d;
  Ilim=0;
  _is_active = false;
}
void PIDcontroller::configure(volatile  float p, volatile  float i, volatile  float d, volatile float lim){
  Kp=p;
  Ki=i;
  Kd=d;
  Ilim=lim;
  _is_active = false;
}
void PIDcontroller::configure(volatile float * pidCoef){
  Kp=pidCoef[0];
  Ki=pidCoef[1];
  Kd=pidCoef[2];
  Ilim=pidCoef[3];
  _is_active = false;
  //Serial.print("PID configured: ");
  //Serial.print(Kp,5);Serial.print(Ki,5);Serial.print(Kd,5);Serial.println(Ilim,5);
}
void PIDcontroller::reset(){
  target=0;
  prevError=0;
  intError=0;
  lastReset=micros();
  _is_active = false;
}
void PIDcontroller::setTarget(volatile float t){
  target=t;
  prevError=0;
  intError=0;
  lastReset=micros();
  //Serial.print("PID target: ");Serial.println(t);
  _is_active = true;
}
bool PIDcontroller::is_active() {
  return _is_active;
}
float PIDcontroller::update(float reading){
  float error,dError;
  //double controlOutput;
  float deltat;
  uint32_t now=micros();

  if (! _is_active) return 0.0;

  error=target-reading;

  if (now-lastReset>300000){
      //reset was more than 0.3 s ago - can use integral and derivative terms
      //otherwise, ignore P and D terms - too much volatility
      deltat=(now-lastUpdate)*0.000001f; //time in seconds
      intError+=error*deltat;
      if (Ilim>0){ //limit the integral error, to prevent integral windup
        if (intError>Ilim) intError=Ilim;
        else if (intError<-Ilim) intError=-Ilim;
      }
      dError=(error-prevError)/deltat;
  }
  lastUpdate=now;
  prevError=error;
  // now, compute the feedback
  float output=Kp*error+Ki*intError+Kd*dError;
  //Serial.print("Kp: "); Serial.println(Kp,4);
  //Serial.print("Target: "); Serial.println(target,4);
  //Serial.print("Error: "); Serial.println(error,4);
  //Serial.print("Deltat: "); Serial.println(deltat,8);
  //Serial.print("Int Error: "); Serial.println(intError,4);
  //Serial.print("D Error: "); Serial.println(dError,4);
  //Serial.print("Kp*Error: "); Serial.println(Kp*error,4);
  //Serial.print("PID output: "); Serial.println(output,4);
  //Serial.print("PID returned: "); Serial.println(controlOutput,4);
  return output;
}

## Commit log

2021-09-27 Initial directory structure created
    [4481_ItsyBitsy_nRF52840.step, pins.xlsx, zumo_mounting_plate.dxf]
2021-10-30 adding hardware files
    Design files for reflectance sensor array
    [blade.dxf, reflectance_sensor_array-BOM.xlsx, reflectance_sensor_array.kicad_pcb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]
2021-10-30 Updated the assembly guide
2021-11-01 hardware files for top plate
    [top_plate-BOM.xlsx, top_plate.kicad_pcb, top_plate.kicad_sch]
2021-11-03 added KiCad files for front array
    [front-array-BOM.xlsx, front-array.kicad_pcb, front-array.kicad_sch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]
2021-11-04 copied mainboard KiCad files
    [mainboard-BOM.xlsx, mainboard-v1.0-BOM.xlsx, mainboard.kicad_pcb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]
2021-11-05 3d modeling update
    [front-array.kicad_pcb, front-array.step, spacer.kicad_pcb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]
2021-11-06 Mainboard: update BOM, fabrication print
    [board frame.stl, mainboard-BOM.xlsx, mainboard.kicad_pcb]
2021-11-24 Major update; version 2.0 almost complete
    [registers.xlsx, top_plate-BOM-JLCPCB.xlsx, top_plate-BOM.xlsx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]
2021-11-29 docs update
    [mainboard-BOM.xlsx, mainboard.kicad_sch]
2022-01-10 Adding IMU code
2022-01-18 firmware update
    [mainboard-BOM-JLCPCB.xlsx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]
2023-10-16 updated python library and docs
    [blade.dxf, front-array.kicad_pcb, front-array.kicad_sch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]
2023-10-28 Creating v4 branch
    [4481_ItsyBitsy_nRF52840.step, BOM-bottom_mid_spacer.csv, BOM-bottom_plate.csv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]
2023-10-28 Updating license information
    [boost.kicad_sch, distance_sensors.kicad_sch, mainboard_dual_battery.kicad_sch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]
2023-10-30 fixing drive and turn issues
    [yozh.py]
2023-11-01 added board package files
    [yozh.cfg]
2023-11-06 added board support package
    [daplink_samd21.cfg, daplink_samd51.cfg, jlink_samd21.cfg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]
2023-11-06 board support update
2023-11-12 board support package
2023-11-15 update arduino support package
2023-11-19 fixing images in docs
    [yozh.py]

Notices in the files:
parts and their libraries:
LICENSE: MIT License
